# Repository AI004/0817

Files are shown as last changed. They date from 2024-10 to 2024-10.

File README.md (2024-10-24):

# 0817

## 网页版查看urdf模型方法

打开网页`https://gkjohnson.github.io/urdf-loaders/javascript/example/bundle/`

将目录`Drawing`下`robot_urdf_12DOF`或`robot_urdf_13DOF`文件夹整体拖入网页中即可打开模型

## webots仿真环境生成

### 步骤

1. 将`urdf`模型转换为`webots`模型，`solidworks`生成`urdf`模型时，`urdf`文件名字为`robot`，在导入`webots`操作时会有冲突

2. 参考`webots_world/adam_lite_simple`中`urdf`文件中，会有关于`world`和`floating_joint`的描述，但被注释，这是正确的，当调用各自目录下`urdf2proto.sh`脚步将`urdf`模型转换为`protos`时，`world`和`floating_joint`应被注释才能顺利执行

   #### 以`DuckDuck-13DOF`为例，执行成功时输出如下

        guobb@pndrobot-REN9000K:~/Documents/GBB/0817/webots_world/DuckDuck-13DOF$ sh urdf2proto.sh
        Robot name: DuckDuck
        Directory "./protos/DuckDuck_textures" already exists!
        Root link: base
        There are 14 links, 13 joints and 0 sensors

3. `webots`中点击`File`,点击`New`,点击`New Project Directory...`新建工程，右键`Add New`添加`PROTO nodes(Webots Projects)`下面`objects`中`floor`,右键`Add New`继续添加`PROTO nodes(Current Project)`中对应执行`urdf2proto.sh`脚步生成的要添加的机器人模型，本例中为`DuckDuck(Robot)`

4. 调整导入的模型在环境中的位置，避免穿模

5. 将生成的模型用于`Control`中时，除此之外，还需要适当修改，如`添加控制器`，`定义模型名称`，更改参考`meshs`文件路径，拷贝`meshs`和`urdf`文件至相应目录等

6. 在`webotsInterface.cpp`中修改`webots`的接口

7. 功能调试

## Control说明

1. 在`./Control/Webots/controllers/mpc_controller/src/webotsInterface.cpp`文件中这一行`Waist = robot->getFromDef("DuckDuck");`中修改模型名称，其中`"DuckDuck"`为`.wbt`文件中定义的机器人模型名称。如果想导入`PND`相关的机器人模型，将`"DuckDuck"`修改为`"Adam"`

2. `DuckDuck`腿部`DH`建模参考链接:<https://blog.csdn.net/qq_60580136/article/details/136062448>

## MatLab

1. 在MatLab计算过程中，计算的结果有 `6.1232e-17` 怎么处理，参考连接:<https://blog.csdn.net/jh1513/article/details/131243390>

2. MatLab计算左腿解析解分下

    1. 把所有变换矩阵都打印出来，参考MATRIX.txt文件
    2. 根据机器人的腿部结构，`关节123`可以抽象为一个`球关节`

        方案一：<span style="color: red; font-weight: bold;">failed</span>

            尝试把`关节123`相对于`base`的变换矩阵整合，观察得到的矩阵，可以看到`T14(3,3)`为`-cos(theta3)`，可以根据单一变量原则计算得到`theta3`，得到theta3后可以根据theta3得到其他，按照矩阵内数据分布可以得到全部的解析解

        方案二：尝试对最后一个变换矩阵求逆<span style="color: red; font-weight: bold;">failed</span>

            1. T16 * T7 = T17
            2. T16_temp = T17 * T7_inv
            3. T16 = T16_temp
            4. T16(3, 2) = cos(theta3)
            5. T16_temp(3, 2) = sin(theta7)
            6. sin(theta7) = cos(theta3)
            结论：
                theta3 = theta7 - pi/2
        方案三：参考链接:<https://blog.csdn.net/fengyu19930920/article/details/81144042> <span style="color: red; font-weight: bold;">failed</span>

            1. DuckDuck的腿部结构符合Pieper准则
            2. 参考UR机械臂逆解方法，把连续三个平行的关节的旋转矩阵单独拎出来，等号左边利用矩阵求逆，构建矩阵相等，观察数据

        方案四：改为MDH模型测试

## Log 说明

### DuckDuck对应的日志说明如下所示

1. 000~000:`时间(以0.0025s递增)`
2. 001~009:`程序内部各部分时间增量`
3. 010~018:`IMURPY角位置` `IMURPY角速度` `IMURPY角加速度`
4. 019~019:`0:start` `1:zero` `2:Z2S` `3:stand` `4:S2W` `5:walk` `6:UniGait` `7:Dual2Single` `8:SingleStand` `9:Single2Dual` `10:stop` `11:swing`
5. 020~020:`各状态时间`
6. 021~041:`q_a`
7. 042~062:`q_dot_a`
8. 063~083:`tau_a`
9. 084~095:`grf`
10. 096~116:`q_c`
11. 117~137:`q_dot_c`
12. 138~156:`tau_c`
13. 159~170:`contact_force`
14. 171~176:`left_foot_position`
15. 177~182:`left_foot_velocity`
16. 183~188:`right_foot_position`
17. 189~194:`right_foot_veloctiy`
18. 195~200:`com_position`
19. 201~206:`com_velocity`
20. 207~212:`body_position`
21. 213~218:`body_velocity`
22. 219~219:`motionTurnOn`
23. 220~220:`motionNumber`
24. 221~221:`momentumTurnOn`
25. 222~222:`carryBoxState`
26. 494~496:`v_body`
27. 497~499:`euler_world`

### DuckDuck对应的关节顺序

1. `left_hip_yaw_joint`
2. `left_hip_roll_joint`
3. `left_hip_pitch_joint`
4. `left_knee_pitch_joint`
5. `left_ankle_pitch_joint`
6. `left_ankle_roll_joint`
7. `right_hip_yaw_joint`
8. `right_hip_roll_joint`
9. `right_hip_pitch_joint`
10. `right_knee_pitch_joint`
11. `right_ankle_pitch_joint`
12. `right_ankle_roll_joint`
13. `throat_pitch_joint`
14. `throat_roll_joint`
15. `throat_yaw_joint`

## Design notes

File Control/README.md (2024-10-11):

## 各版本使用及注意事项描述

### webots可用版本
adam_lite.urdf

adam_standard.urdf

standard_plus23.urdf

standard_plus29.urdf

### 实机可用版本
adam_lite.urdf

adam_standard.urdf（未测试）

standard_plus23.urdf

standard_plus29.urdf

### urdf文件对应webots仿真环境描述
adam_lite.urdf - adam_lite_v1.1_world.wbt

adam_standard.urdf - adam_standard_world.wbt

standard_plus23.urdf - adma_standard_plus_23dof_world.wbt

standard_plus29.urdf - adma_standard_plus_29dof_world.wbt

standard_plus53.urdf - adma_standard_plus_53dof_world.wbt

### 使用方法
`webots` 仿真时更换`Sources/config/pnc_config_sim.json`中`"urdf"`标签即可

`实机运行时更换` Sources/config/pnc_config_sim.json中`"urdf"`标签即可

# 功能说明

## dataPub
添加dataPub模块，进行机器人状态数据发布。可在dataPub中添加自定义数据发布，实时监看更多机器人相关状态。具体话题发布于定义见`dataPub.cpp`。
`main.cpp`中使用`#define ROS_PUB`打开机器人数据话题发布。

## rqt_multiplot
安装对应ubuntu版本`rqt_multiplot`，启动`roscore`后，另起终端输入：
```
rqt_multiplot
```
打开`plot`文件夹中的.xml文件即可查看对应机器人状态绘图。在`dataPub.cpp`修改想要使用的话题与发布的数据相关，自定义.xml文件实现自己需求的数据实时绘图监看。

## example
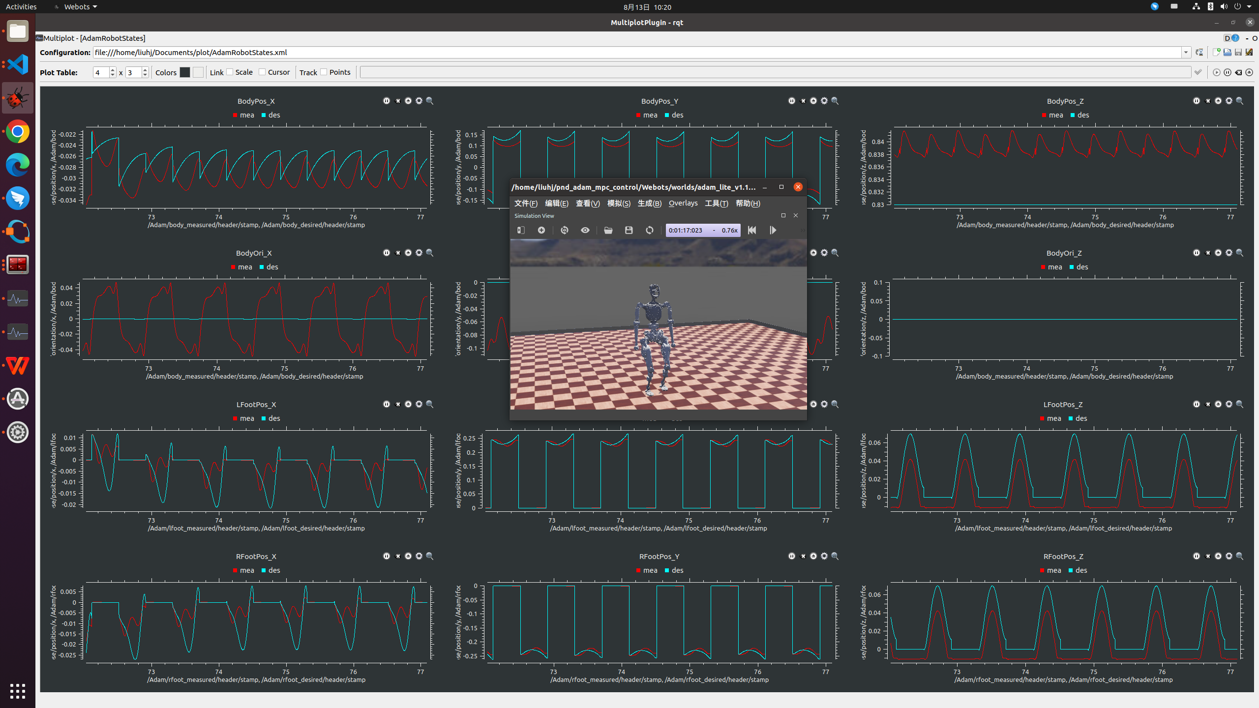
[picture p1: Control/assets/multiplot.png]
multiplot


## 基于角动量的落足点计算
首先使用rbdl进行质心处角动量计算，详见函数`estCOMStateMomentum()`,然后使用`footholdPlan_AM()`计算落足点。打开`pnc_config_sim.json`的`use_AM_calcFootHold`启用基于接触点角动量的落足点规划。同时新加入两个相关的落足点调整参数，`l_start_offset`,`r_start_offset`,加大该偏置可以调整落足点选取，调节以达到期望的侧向落足宽度。

## 角动量数据处理
收到外部干扰时角动量可能存在脉冲突变，使用一个中值滤波器进行脉冲处理，详见`updateDataAndProcessPulse`及`calculateMedian`函数。
真机上采集到的角动量数据噪音较大，故采用与`q_dot_a`同截止频率的低通滤波器进行滤波处理，打开`#define MOMENTUM_FILT`开关即可使用。

### reference
Gong, Yukai, and Jessy Grizzle. "Angular momentum about the contact point for control of bipedal locomotion: Validation in a lip-based controller." arXiv preprint arXiv:2008.10763 (2020).

Gong, Yukai, and Jessy W. Grizzle. "Zero dynamics, pendulum models, and angular momentum in feedback control of bipedal locomotion." Journal of Dynamic Systems, Measurement, and Control 144.12 (2022): 121006.

## push recovery
`state.cpp`中打开`momentumTurnOn`开关，打开`pnc_config_sim.json`的`use_AM_calcFootHold`开关。当机器人位于`stand`状态时，监测外力冲击及扰动，实时可切换进入`uniGait`状态，随后再切回站立状态。

### xbox
更新到使用xbox手柄切换`momentumTurnOn`开关，按下右摇杆按键即可切换。

#### xbox bug
手柄摇杆按键键值映射错误，已修正。
手柄键值存在抖动，状态切换时无影响，但是使用键值突变作为状态位切换时需注意锁存一个flag作为标志，防止抖动导致状态切换异常。

### world
新增一个添加有摆锤的仿真世界，世界名为`adma_standard_plus_23dof_withPendulum.wbt`，可从中复制摆锤添加到本地世界中使用。
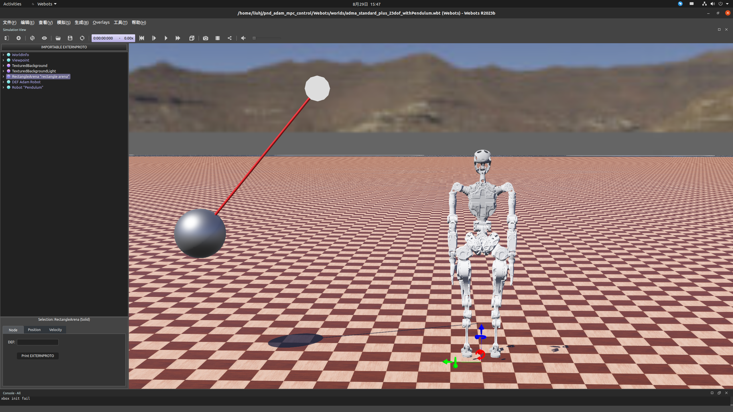
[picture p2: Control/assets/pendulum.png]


##
### 依赖环境
Eigen - https://gitlab.com/libeigen/eigen/-/archive/3.4.0/eigen-3.4.0.tar.gz

rbdl - https://github.com/rbdl/rbdl

qpOASES - https://github.com/coin-or/qpOASES.git

libtorch - https://download.pytorch.org/libtorch/cpu/libtorch-cxx11-abi-shared-with-deps-1.12.1%2Bcpu.zip

qt - sudo apt install qtbase5-dev

### 编译运行

#### Webots
编译： `sh buildwebotsim.sh`

清理： `sh cleanwebotsim.sh`

webots world: Webots/worlds/humanoid_test.wbt

#### 真机
编译： `sh buildrobot.sh`

清理： `sh cleanrobot.sh`

运行： `sh run.sh`

### 程序架构
#### example / Webots 
分别放置了上机和仿真的`main.cpp`

#### RobotControl:

`Robot_Constructor` 为机器人的RBDL建模

`Estimation_Operator`、`KalmanFilter` 为机器人的状态估计

`wbc_solver` 为WBC的求解

`MomentumController` 为原地抗干扰的动量控制

#### RobotInterface:

`JointInterface` 为关节控制接口

`S2P` 为脚踝的串并联转换

`wrist_S2P` 为手腕的串并联转换

`RobotInterfaceImpl` 为机器人获取状态和发送指令的具体实现，以及读绝编等

#### Sources

`joint_pd_config` 为关节的PD参数设置
`joint_abs_config` 为关节的零位
`pnc_config` 和 `pnc_config_sim` 分别是真机和仿真的WBC控制参数

`motion` 为原地动作的数据

`python_scripts` 为读绝编、设置零位的python脚本

#### StateMachine

`joystick` 为遥控器的代码

`State` 为回零、站立、行走等状态的具体实现

### 构型更改

在`Robot_Constructor`中调整`nbody`的数量，并参考现有代码填写新连杆的质心、重量惯量等参数

现有程序控制关节数量为23，将需要修改的地方替换成新关节数量

修改构型 WBC 控制算法一般无须调整，只要保证任务维度正确即可

### WBC控制

现有WBC采取对不同任务赋予不同权重的方式调整相对优先级，目前定义了5个任务：
`body_task` 为盆骨位姿任务，
`com_task` 为质心位姿任务，
`left_foot` 为左脚位姿任务，
`right_foot` 为右脚位姿任务，
`upper_joints` 为3个腰关节+8个手臂关节的关节角任务

其中盆骨、质心、左右脚的位姿均为工作空间的量，不因构型不同而变化，只需对上身关节角任务作相应调整

各任务的初始权重和PD参数在 `pnc_config` 中设定，在 `State.cpp` 各状态的 `OnEnter` 和 `run` 中会对各任务的权重做重新分配

KP/KD 1~6 的顺序是 roll pitch yaw x y z 

各关节的力矩上限和足底力上限通过 `WbcSolver::SetConstraints` 设定

`robotdata->q_a` `robotdata->q_dot_a` `robotdata->tau_a` 分别为关节的当前位置、速度和力矩

`robotdata->q_c` `robotdata->q_dot_c` `robotdata->tau_c` 分别为关节的期望位置、速度和力矩

`robotdata->q_factor` `robotdata->q_dot_factor` 分别为关节位置和速度的控制强度，从0到1控制强度逐渐变强

### Reference

Feng S, Whitman E, Xinjilefu X, et al. Optimization‐based full body control for the darpa robotics challenge[J]. Journal of field robotics, 2015, 32(2): 293-312.

Apgar T, Clary P, Green K, et al. Fast Online Trajectory Optimization for the Bipedal Robot Cassie[C]//Robotics: Science and Systems. 2018, 101: 14.

Moro F L, Sentis L. Whole-body control of humanoid robots[J]. Humanoid Robotics: A reference, Springer, Dordrecht, 2019.

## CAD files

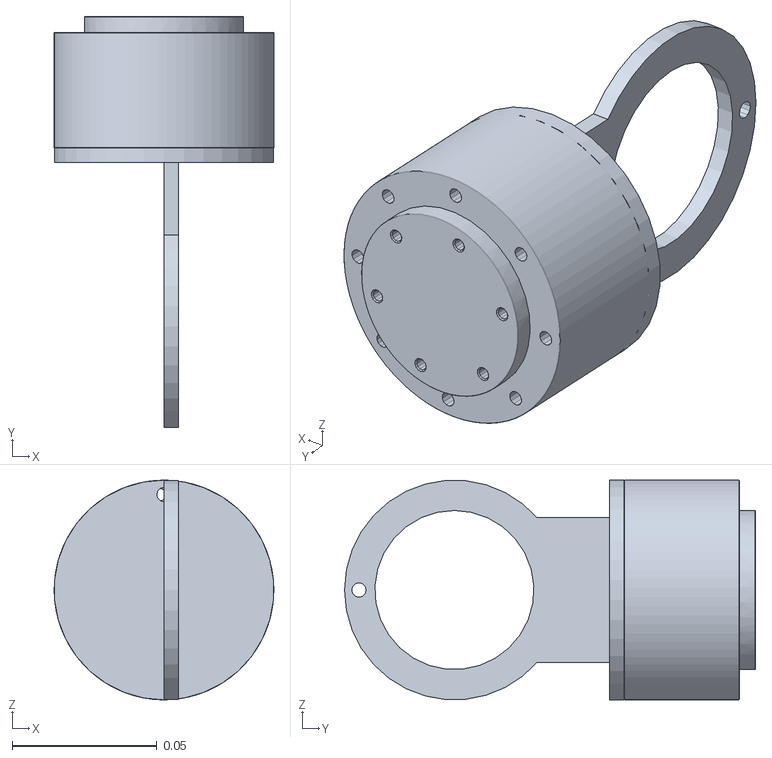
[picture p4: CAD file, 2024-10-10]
Control/Webots/meshes_DuckDuck/left_hip_roll.STL
0.076 x 0.142 x 0.076

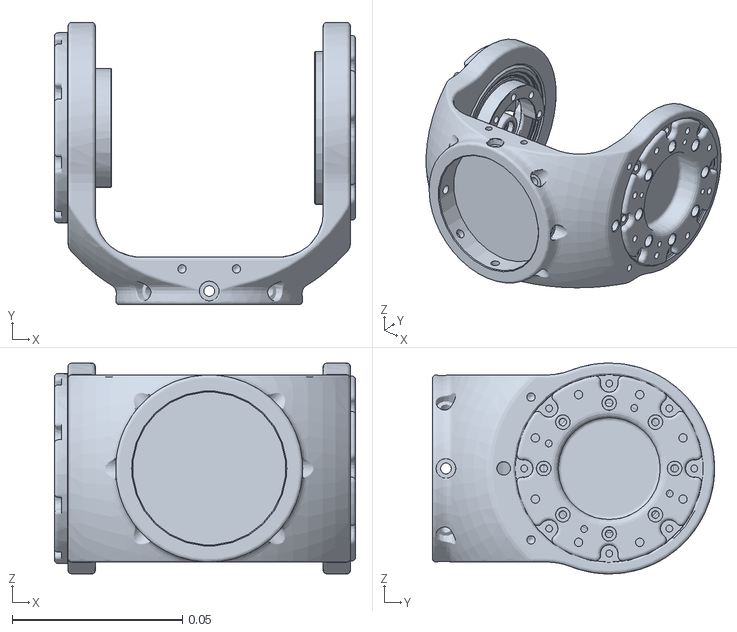
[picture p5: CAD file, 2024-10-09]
Control/Webots/meshes_lite_simple/shoulderPitchLeft.STL
0.0885 x 0.083 x 0.062

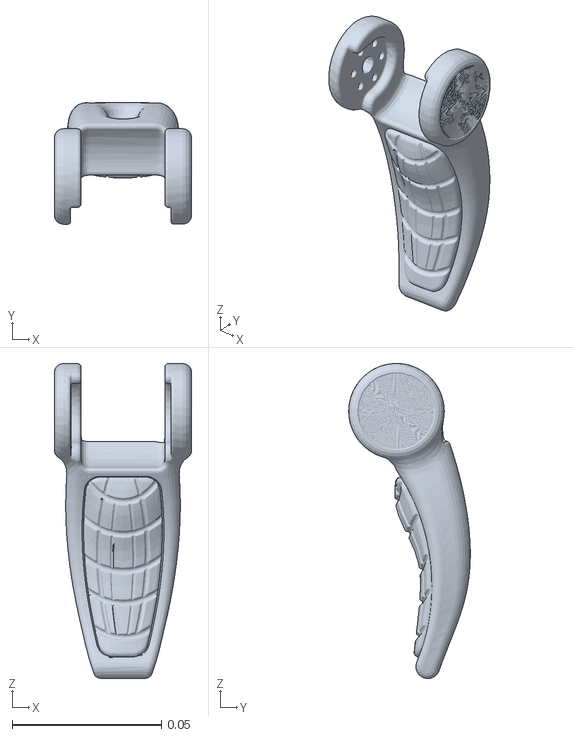
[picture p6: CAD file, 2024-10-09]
Control/Webots/meshes_standard/gripperRight.STL
0.046 x 0.0407 x 0.105

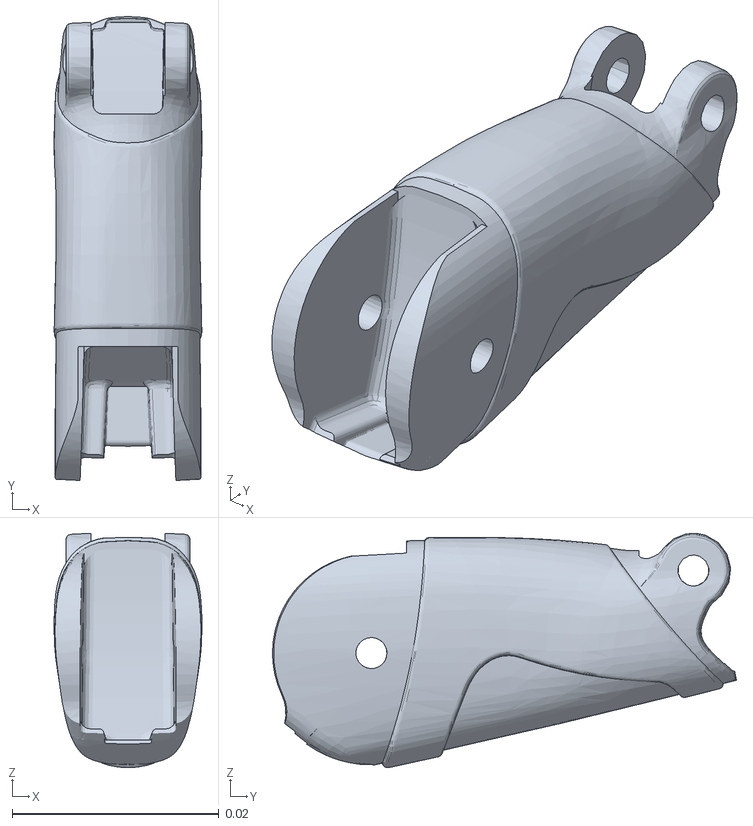
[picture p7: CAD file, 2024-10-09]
Control/Webots/meshes_standard_plus/R_ring_proximal.STL
0.0143 x 0.0449 x 0.0227

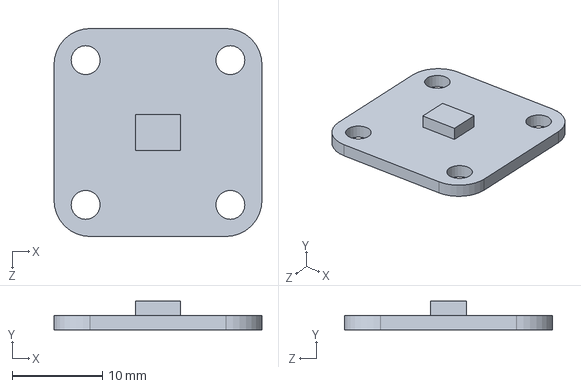
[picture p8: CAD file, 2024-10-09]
Drawing/branch struct/BLDC base/AS5600.SLDPRT
23.0 x 3.20 x 23.0 mm

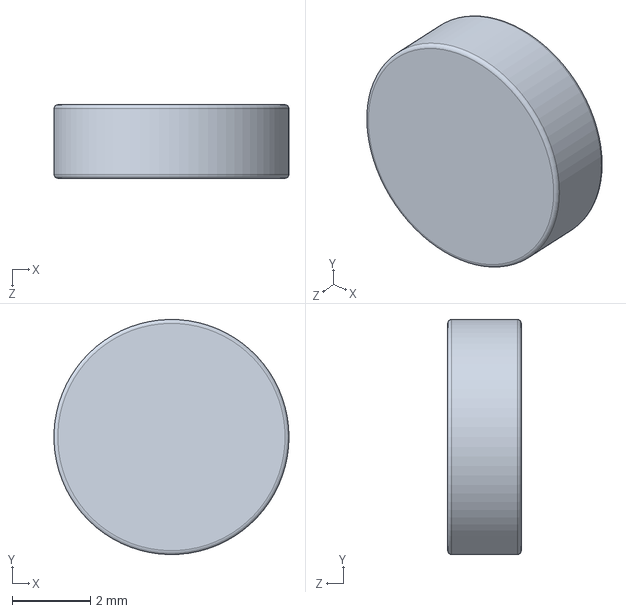
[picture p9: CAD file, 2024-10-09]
Drawing/branch struct/CycloidalDrive - v0.3.0/magnetic.SLDPRT
6.00 x 6.00 x 1.88 mm

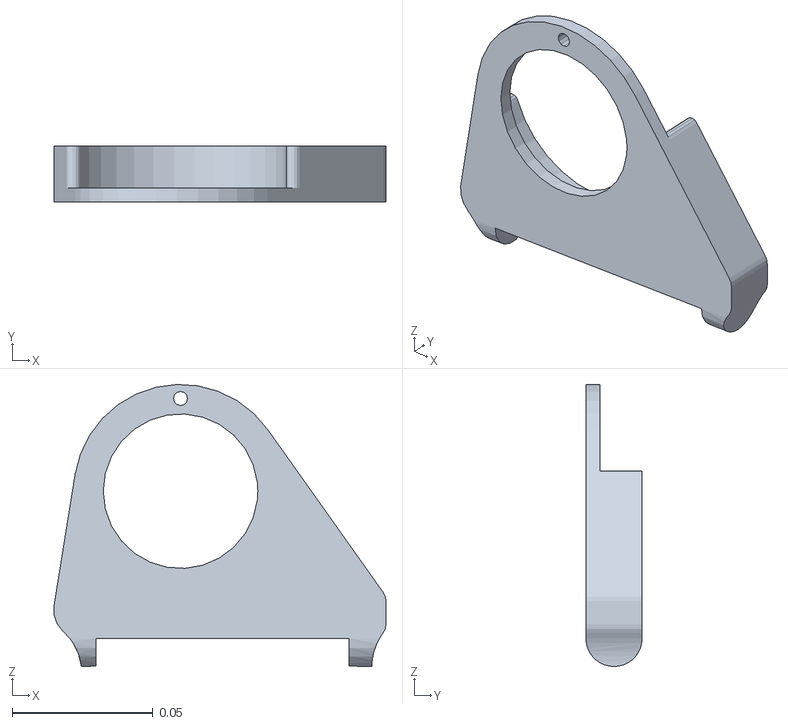
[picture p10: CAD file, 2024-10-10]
webots_world/DuckDuck-15DOF/meshes/right_ankle_pitch.STL
0.118 x 0.02 x 0.1

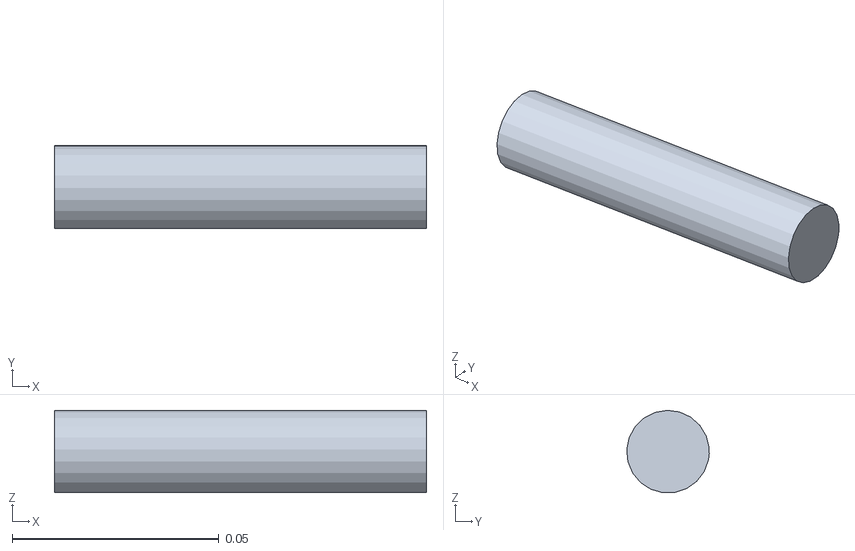
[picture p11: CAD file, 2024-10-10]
Control/Webots/meshes_DuckDuck/right_ankle_roll.STL
0.09 x 0.02 x 0.0199

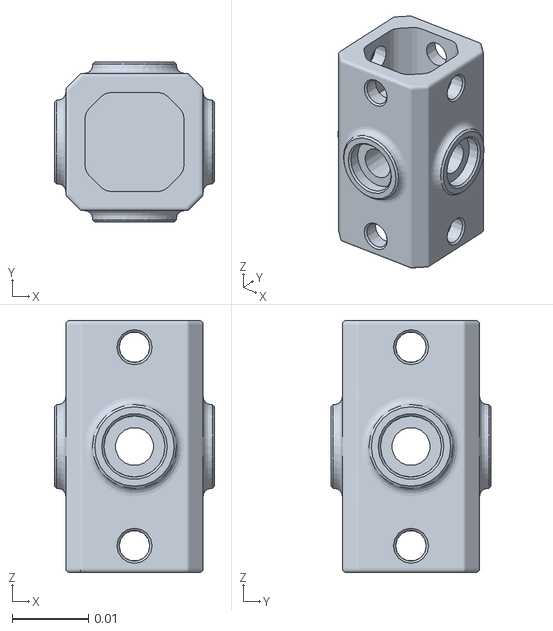
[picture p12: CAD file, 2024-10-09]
Control/Webots/meshes_lite_simple/anklePitchLeft.STL
0.021 x 0.021 x 0.033

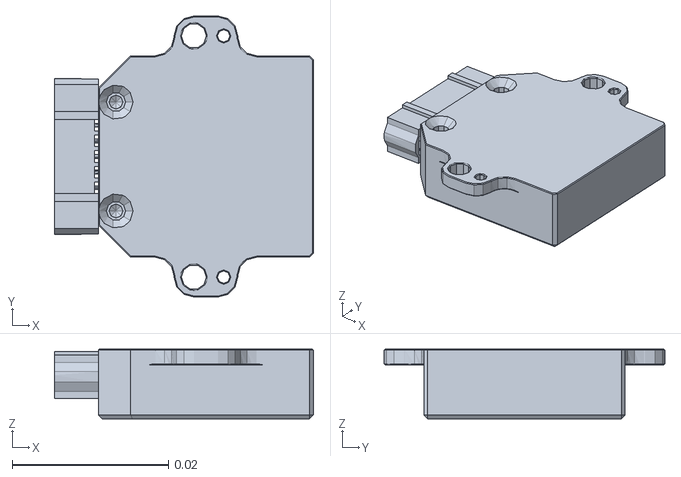
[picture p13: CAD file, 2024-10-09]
Control/Webots/meshes_standard/vn100-0001.stl
0.0331 x 0.0359 x 0.00892

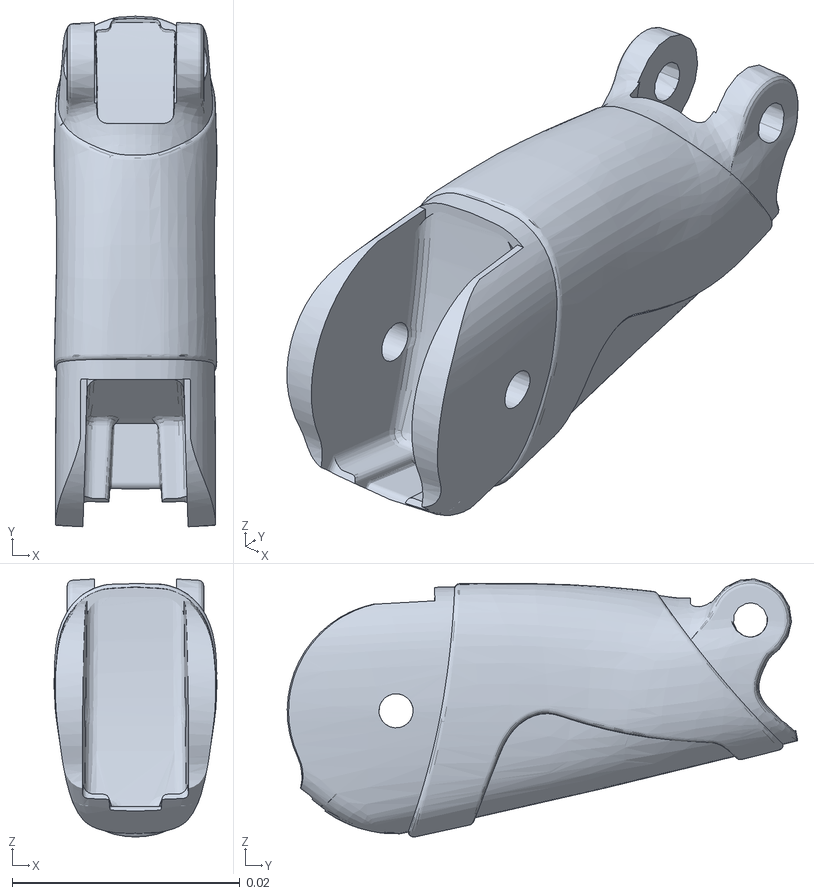
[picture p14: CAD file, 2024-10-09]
Control/Webots/meshes_standard_plus/R_index_distalR_middle_proximal.STL
0.0143 x 0.0449 x 0.0227

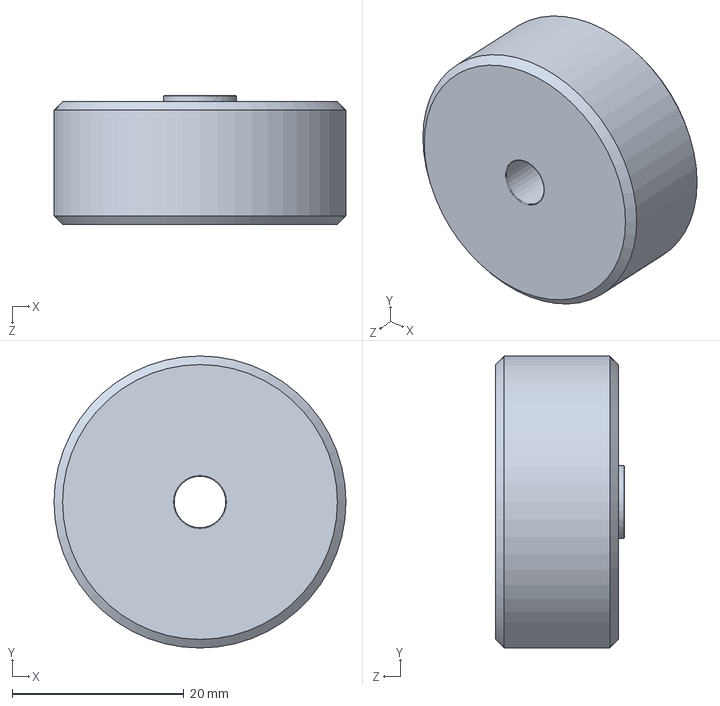
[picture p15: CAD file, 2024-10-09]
Drawing/branch struct/BLDC base/motor.SLDPRT
34.0 x 34.0 x 15.0 mm

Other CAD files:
Drawing/robot/DuckDuck.SLDASM
Drawing/branch struct/BLDC base/assembly.SLDASM
Drawing/robot/DuckDuck_Init_Position.SLDASM
Drawing/branch struct/CycloidalDrive - v0.3.0/装配体-总装.SLDASM
Drawing/branch struct/CycloidalDrive - v0.3.0/装配体-零件组合.SLDASM
Drawing/branch struct/CycloidalDrive - v0.3.0/装配体-爆炸结构.SLDASM
Control/Webots/meshes_DuckDuck/base.STL
Control/Webots/meshes_DuckDuck/left_ankle_pitch.STL
Control/Webots/meshes_DuckDuck/left_ankle_roll.STL
Control/Webots/meshes_DuckDuck/left_hip_pitch.STL
Control/Webots/meshes_DuckDuck/left_hip_yaw.STL
Control/Webots/meshes_DuckDuck/left_knee_pitch.STL
Control/Webots/meshes_DuckDuck/right_hip_pitch.STL
Control/Webots/meshes_DuckDuck/right_hip_roll.STL
Control/Webots/meshes_DuckDuck/right_hip_yaw.STL
Control/Webots/meshes_DuckDuck/throat_pitch.STL
Control/Webots/meshes_DuckDuck/throat_roll.STL
Control/Webots/meshes_DuckDuck/throat_yaw.STL
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

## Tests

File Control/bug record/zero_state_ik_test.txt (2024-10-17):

INFO: mpc_controller: Starting controller: /home/guobb/Documents/GBB/0817/Control/Webots/controllers/mpc_controller/mpc_controller
using urdf:./Sources/urdf/DuckDuck.urdf
DuckDuck
Bodies:
  Body ID: 0, Name: ROOT
  Body ID: 1, Name: base_Translate
  Body ID: 2, Name: base
  Body ID: 3, Name: left_hip_yaw
  Body ID: 4, Name: left_hip_roll
  Body ID: 5, Name: left_hip_pitch
  Body ID: 6, Name: left_knee_pitch
  Body ID: 7, Name: left_ankle_pitch
  Body ID: 8, Name: left_ankle_roll
  Body ID: 9, Name: neck_pitch
  Body ID: 10, Name: neck_roll
  Body ID: 11, Name: neck_yaw
  Body ID: 12, Name: right_hip_yaw
  Body ID: 13, Name: right_hip_roll
  Body ID: 14, Name: right_hip_pitch
  Body ID: 15, Name: right_knee_pitch
  Body ID: 16, Name: right_ankle_pitch
  Body ID: 17, Name: right_ankle_roll
robotdata->ndof: 21
robotdata->robot_model->mBodies.size(): 18
i: 0 2
i: 1 3
i: 2 4
i: 3 5
i: 4 6
i: 5 7
i: 6 8
i: 7 9
i: 8 10
i: 9 11
i: 10 12
i: 11 13
i: 12 14
i: 13 15
i: 14 16
i: 15 17
i: 16 18
i: 17 19
robotdata->task_card_set[0]->joint_id: 8
robotdata->task_card_set[1]->joint_id: 17
robotdata->task_card_set[2]->joint_id: 2
robotdata->task_card_set[3]->joint_id: 2
robotdata->task_card_set[4]->joint_id: 17
robotdata->task_card_set[5]->joint_id: 7
ndof: 21
Swing
Started 
xbox connect!
version: 1.4.0
Started!
To Zero
left leg jacobi:
           0            0            0            1            0  3.72529e-05  3.72529e-05            1  1.07986e-06  1.07986e-06  1.07986e-06            1            0            0            0            0            0            0            0            0            0
           0            0            0  2.06795e-25            1 -2.60325e-05 -2.60325e-05 -1.07803e-06            1            1            1 -1.07968e-06            0            0            0            0            0            0            0            0            0
           0            0            0  6.77626e-21  2.60325e-05            1            1 -3.72529e-05  4.89317e-05  4.89317e-05  4.89317e-05 -3.63101e-06            0            0            0            0            0            0            0            0            0
           1            0            0 -8.47033e-22     -0.33239    -0.133626   -0.0936258  3.84648e-06    -0.332392    -0.192392   -0.0523924 -1.27055e-21            0            0            0            0            0            0            0            0            0
           0            1            0     0.332387 -1.50978e-10  6.58279e-06  6.58283e-06     0.332388  3.58648e-07  2.07646e-07   5.6567e-08  2.95309e-17            0            0            0            0            0            0            0            0            0
           0            0            1     0.133634  5.79958e-06  4.97812e-06    3.488e-06    0.0936344  5.90069e-06  2.26128e-06  1.90237e-07  2.77556e-17            0            0            0            0            0            0            0            0            0
right leg jacobi:
           0            0            0            1            0  3.72529e-05            0            0            0            0            0            0            0            0            0 -3.72529e-05           -1  -1.1177e-05  -1.1177e-05  -1.1177e-05           -1
           0            0            0  2.06795e-25            1 -2.60325e-05            0            0            0            0            0            0            0            0            0  2.60325e-05 -1.11784e-05            1            1            1 -1.11783e-05
           0            0            0  6.77626e-21  2.60325e-05            1            0            0            0            0            0            0            0            0            0           -1  3.72526e-05  3.72444e-05  3.72444e-05  3.72444e-05  3.50987e-05
           1            0            0            0    -0.332393     0.133614            0            0            0            0            0            0            0            0            0   -0.0936144   7.2027e-06    -0.332392    -0.192392   -0.0523924  4.23516e-22
           0            1            0     0.332397  -2.8436e-10  1.45948e-06            0            0            0            0            0            0            0            0            0 -1.45944e-06    -0.332396 -3.71559e-06 -2.15062e-06 -5.85657e-07  1.12154e-17
           0            0            1    -0.133606  1.09233e-05 -4.97748e-06            0            0            0            0            0            0            0            0            0  3.48737e-06    0.0936058  1.19695e-05  6.75342e-06   1.8389e-06  2.77556e-17
head jacobi:
0 0 0 0 0 0 0 0 0 0 0 0 1 0 0 0 0 0 0 0 0
0 0 0 0 0 0 0 0 0 0 0 0 0 1 0 0 0 0 0 0 0
0 0 0 0 0 0 0 0 0 0 0 0 0 0 1 0 0 0 0 0 0

==============================================================================================================================
==============================================================VS==============================================================
==============================================================================================================================

model->dof_count: 21
model->mBodies.size(): 18
model->gravity:     0     0 -9.81
Joints:
  ROOT
  base_Translate
  base
  left_hip_yaw
  left_hip_roll
  left_hip_pitch
  left_knee_pitch
  left_ankle_pitch
  left_ankle_roll
  neck_pitch
  neck_roll
  neck_yaw
  right_hip_yaw
  right_hip_roll
  right_hip_pitch
  right_knee_pitch
  right_ankle_pitch
  right_ankle_roll
Bodies:
  Body ID: 0, Name: ROOT
  Body ID: 1, Name: base_Translate
  Body ID: 2, Name: base
  Body ID: 3, Name: left_hip_yaw
  Body ID: 4, Name: left_hip_roll
  Body ID: 5, Name: left_hip_pitch
  Body ID: 6, Name: left_knee_pitch
  Body ID: 7, Name: left_ankle_pitch
  Body ID: 8, Name: left_ankle_roll
  Body ID: 9, Name: neck_pitch
  Body ID: 10, Name: neck_roll
  Body ID: 11, Name: neck_yaw
  Body ID: 12, Name: right_hip_yaw
  Body ID: 13, Name: right_hip_roll
  Body ID: 14, Name: right_hip_pitch
  Body ID: 15, Name: right_knee_pitch
  Body ID: 16, Name: right_ankle_pitch
  Body ID: 17, Name: right_ankle_roll
Q: 0 0 0 0 0 0 0 0 0 0 0 0 0 0 0 0 0 0 0 0 0
QDot: 0 0 0 0 0 0 0 0 0 0 0 0 0 0 0 0 0 0 0 0 0
Tau: 0 0 0 0 0 0 0 0 0 0 0 0 0 0 0 0 0 0 0 0 0
QDDot:  2.22045e-16 -1.38778e-17        -9.81 -7.07298e-17  -6.6653e-16 -1.08278e-17  1.99807e-15   9.5483e-17  1.06981e-15 -4.55485e-16 -9.72608e-17 -2.47532e-17 -1.76993e-16 -5.64579e-17  1.03078e-17  2.01833e-15 -1.51671e-16  1.03713e-15 -4.20304e-16 -1.29301e-16  8.09414e-17
Q: 0 0 0 0 0 0 0 0 0 0 0 0 0 0 0 0 0 0 0 0 0
QDot: 0 0 0 0 0 0 0 0 0 0 0 0 0 0 0 0 0 0 0 0 0
Tau:  4.95859e-16 -3.44709e-17  5.25285e-17 -5.29631e-34  4.10464e-33 -5.00742e-33 -1.92593e-33 -2.94908e-34 -1.46175e-33  4.81482e-35  2.25695e-36 -2.18328e-39  7.02964e-33 -7.89932e-35 -6.77085e-36  4.81482e-34  7.46298e-34  1.32144e-33            0  5.64237e-36 -1.26091e-38
QDDot:  2.22045e-16 -1.38778e-17        -9.81 -7.07298e-17  -6.6653e-16 -1.08278e-17  1.99807e-15   9.5483e-17  1.06981e-15 -4.55485e-16 -9.72608e-17 -2.47532e-17 -1.76993e-16 -5.64579e-17  1.03078e-17  2.01833e-15 -1.51671e-16  1.03713e-15 -4.20304e-16 -1.29301e-16  8.09414e-17
Body Transform (Base to Body 8):
        1         0         0         0
        0         1         0  0.133618
        0         0         1 -0.332392
        0         0         0         1
Jacobian Matrix (Body 8):
         0          0          0          1          0          0          0          1          0          0          0          1          0          0          0          0          0          0          0          0          0
         0          0          0          0          1          0          0          0          1          1          1          0          0          0          0          0          0          0          0          0          0
         0          0          0          0          0          1          1          0          0          0          0          0          0          0          0          0          0          0          0          0          0
         1          0          0          0  -0.332392  -0.133618 -0.0936182          0  -0.332392  -0.192392 -0.0523924          0          0          0          0          0          0          0          0          0          0
         0          1          0   0.332392          0          0          0   0.332392          0          0          0          0          0          0          0          0          0          0          0          0          0
         0          0          1   0.133618          0          0          0  0.0936182          0          0          0          0          0          0          0          0          0          0          0          0          0
Jacobian Matrix (Body 17):
         0          0          0          1          0          0          0          0          0          0          0          0          0          0          0          0         -1          0          0          0         -1
         0          0          0          0          1          0          0          0          0          0          0          0          0          0          0          0          0          1          1          1          0
         0          0          0          0          0          1          0          0          0          0          0          0          0          0          0         -1          0          0          0          0          0
         1          0          0          0  -0.332392   0.133618          0          0          0          0          0          0          0          0          0 -0.0936182          0  -0.332392  -0.192392 -0.0523924          0
         0          1          0   0.332392          0          0          0          0          0          0          0          0          0          0          0          0  -0.332392          0          0          0          0
         0          0          1  -0.133618          0          0          0          0          0          0          0          0          0          0          0          0  0.0936182          0          0          0          0
Jacobian Matrix (Body 11):
     0      0      0      0      0      0 0.0025      0      0      0      0      0      0 0.1385      0      0      0      0      0      0      0
     0      0      0      0      1      0 0.0775      0      0      0      0      0      1      0  0.061      0      0      0      0      0      0
     0      0      0      1      0      1      0      0      0      0      0      0      0      0      0      0      0      0      0      0      0
model->q_size: 21
error: 0.148857  0.0811659   0.119197  0.0284271 -0.0144422     0.0154  0.0104289
error: 0.0279139         0.00167909  -0.0043331   0.0274701 0.000301794 0.000831977 -0.00148235
error: 0.0101265          0.00681823  -0.00741633  -0.00101897  8.48899e-06 -4.85448e-05 -0.000120378
error: 0.00206528        0.000235621 -3.20301e-06  -0.00205179 -5.53563e-07  1.15344e-07 -2.16779e-06
error: 0.000729142      -0.000479004  0.000549417 -1.85808e-05 -3.54857e-08 -2.86412e-07 -1.78004e-07
error: 0.000158336      -4.00638e-05  2.49869e-05  0.000151132 -2.14527e-09  -1.0211e-09 -1.37429e-08
error: 5.25969e-05       3.37228e-05 -3.95292e-05  8.16398e-06 -2.09217e-10  -1.3553e-09 -1.06313e-09
error: 1.22543e-05       4.47633e-06 -3.62638e-06 -1.08158e-05 -1.17184e-11 -2.30812e-11 -6.94363e-11
error: 3.75225e-06      -2.29376e-06  2.76204e-06 -1.09049e-06 -1.16395e-12 -5.97994e-12 -6.23163e-12
error: 9.52502e-07      -4.34401e-07  3.92544e-07  7.51309e-07 -6.28317e-14 -2.41973e-13 -3.51608e-13
Inverse Kinematics Converged in 9 iterations.
Function took 0.616268 milliseconds
Inverse Kinematics Result:   0.14966  0.150027 -0.449909   0.50081  0.147031  0.149633

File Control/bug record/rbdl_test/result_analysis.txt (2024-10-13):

-- Found RBDL: /usr/local/lib/librbdl.so
-- Configuring done
-- Generating done
-- Build files have been written to: /home/g/Documents/0817/Control/bug record/rbdl_test/build
Scanning dependencies of target read_urdf
[ 25%] Building CXX object CMakeFiles/read_urdf.dir/read_urdf.cpp.o
[ 75%] Built target example
[100%] Linking CXX executable read_urdf
[100%] Built target read_urdf
model->dof_count: 21
model->mBodies.size(): 18
model->gravity:     0     0 -9.81
Joints:
  ROOT
  base_Translate
  base
  left_hip_yaw
  left_hip_roll
  left_hip_pitch
  left_knee_pitch
  left_ankle_pitch
  left_ankle_roll
  neck_pitch
  neck_roll
  neck_yaw
  right_hip_yaw
  right_hip_roll
  right_hip_pitch
  right_knee_pitch
  right_ankle_pitch
  right_ankle_roll
Bodies:
  Body ID: 0, Name: ROOT
  Body ID: 1, Name: base_Translate
  Body ID: 2, Name: base
  Body ID: 3, Name: left_hip_yaw
  Body ID: 4, Name: left_hip_roll
  Body ID: 5, Name: left_hip_pitch
  Body ID: 6, Name: left_knee_pitch
  Body ID: 7, Name: left_ankle_pitch
  Body ID: 8, Name: left_ankle_roll
  Body ID: 9, Name: neck_pitch
  Body ID: 10, Name: neck_roll
  Body ID: 11, Name: neck_yaw
  Body ID: 12, Name: right_hip_yaw
  Body ID: 13, Name: right_hip_roll
  Body ID: 14, Name: right_hip_pitch
  Body ID: 15, Name: right_knee_pitch
  Body ID: 16, Name: right_ankle_pitch
  Body ID: 17, Name: right_ankle_roll
Q: 0 0 0 0 0 0 0 0 0 0 0 0 0 0 0 0 0 0 0 0 0
QDot: 0 0 0 0 0 0 0 0 0 0 0 0 0 0 0 0 0 0 0 0 0
Tau: 0 0 0 0 0 0 0 0 0 0 0 0 0 0 0 0 0 0 0 0 0
QDDot:  2.22045e-16 -1.38778e-17        -9.81 -7.07298e-17  -6.6653e-16 -1.08278e-17  1.99807e-15   9.5483e-17  1.06981e-15 -4.55485e-16 -9.72608e-17 -2.47532e-17 -1.76993e-16 -5.64579e-17  1.03078e-17 -2.01833e-15  1.51671e-16 -1.03713e-15  4.20304e-16  1.29301e-16 -8.09414e-17
Q: 0 0 0 0 0 0 0 0 0 0 0 0 0 0 0 0 0 0 0 0 0
QDot: 0 0 0 0 0 0 0 0 0 0 0 0 0 0 0 0 0 0 0 0 0
Tau:  4.95859e-16 -3.44709e-17  5.25285e-17 -5.29631e-34  4.10464e-33 -5.00742e-33 -1.92593e-33 -2.94908e-34 -1.46175e-33  4.81482e-35  2.25695e-36 -2.18328e-39  7.02964e-33 -7.89932e-35 -6.77085e-36 -4.81482e-34 -7.46298e-34 -1.32144e-33           -0 -5.64237e-36  1.26091e-38
QDDot:  2.22045e-16 -1.38778e-17        -9.81 -7.07298e-17  -6.6653e-16 -1.08278e-17  1.99807e-15   9.5483e-17  1.06981e-15 -4.55485e-16 -9.72608e-17 -2.47532e-17 -1.76993e-16 -5.64579e-17  1.03078e-17 -2.01833e-15  1.51671e-16 -1.03713e-15  4.20304e-16  1.29301e-16 -8.09414e-17
Body Transform (Base to Body 11):
       1        0        0   0.0775
       0        1        0  -0.0025
       0        0        1 0.247375
       0        0        0        1
Jacobian Matrix (Body 11):
        1         0         0         0  0.247375    0.0025         0         0         0         0         0         0    0.1385         0         0         0         0         0         0         0         0
        0         1         0 -0.247375         0    0.0775         0         0         0         0         0         0         0     0.061         0         0         0         0         0         0         0
        0         0         1   -0.0025   -0.0775         0         0         0         0         0         0         0         0         0         0         0         0         0         0         0         0
        0         0         0         0         0         0         0         0         0         0         0         0         0         0         0         0         0         0         0         0         0
        0         0         0         0         0         0         0         0         0         0         0         0         0         0         0         0         0         0         0         0         0
        0         0         0         0         0         0         0         0         0         0         0         0         0         0         0         0         0         0         0         0         0
read_urdf: /usr/local/include/eigen3/Eigen/src/Core/SolverBase.h:151: void Eigen::SolverBase<Derived>::_check_solve_assertion(const Rhs&) const [with bool Transpose_ = false; Rhs = Eigen::MatrixBase<Eigen::Matrix<double, 3, 1> >; Derived = Eigen::ColPivHouseholderQR<Eigen::Matrix<double, -1, -1, 1, -1, -1> >]: Assertion `(Transpose_?derived().cols():derived().rows())==b.rows() && "SolverBase::solve(): invalid number of rows of the right hand side matrix b"' failed.
Aborted (core dumped)
g@g:~/Documents/0817/Control/bug record/rbdl_test$

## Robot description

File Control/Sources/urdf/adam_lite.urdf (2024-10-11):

<?xml version="1.1" encoding="utf-8"?>
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
<robot name="adam_lite">
  <link name="world"/>
  <link name="pelvis">
    <inertial>
      <origin xyz="-0.00120281 -0.00000119 -0.00802155" rpy="0 0 0" />
      <mass value="10.18730021" />
      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
    </inertial>
    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
  </link>
  <joint name="floating_joint" type="floating">
    <parent link="world"/> 
    <child link="pelvis"/>
    <origin xyz="0 0 0" rpy="0 0 0"/>
    <axis xyz="0 0 0 1 0 0" />
    <axis xyz="0 0 0 0 1 0" />
    <axis xyz="0 0 0 0 0 1" />
    <axis xyz="1 0 0" />
    <axis xyz="0 1 0" />
    <axis xyz="0 0 1" />
  </joint>
  <link name="hipPitchLeft">
    <inertial>
      <origin xyz="-0.05818187 0.05889478 -0.00031205" rpy="0 0 0" />
      <mass value="2.15124786" />
      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
    </inertial>
    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
  </link>
  <joint name="hipPitch_Left" type="revolute">
    <origin xyz="0 0.096192 -0.033241" rpy="-0.61087 0 0" />
    <parent link="pelvis" />
    <child link="hipPitchLeft" />
    <axis xyz="0 1 0" />
    <limit effort="230.0" lower="-2.09" upper="2.09" velocity="15.0"/>
  </joint>
  <link name="hipRollLeft">
    <inertial>
      <origin xyz="0.03995412 -0.00011618 -0.01102103" rpy="0 0 0" />
      <mass value="1.29421887" />
      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
    </inertial>
    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
  </link>
  <joint name="hipRoll_Left" type="revolute">
    <origin xyz="-0.0255 0.069 0" rpy="0.61087 0 0" />
    <parent link="hipPitchLeft" />
    <child link="hipRollLeft" />
    <axis xyz="1 0 0" />
    <limit effort="160.0" lower="-0.78" upper="1.57" velocity="8.0"/>
  </joint>
  <link name="thighLeft">
    <inertial>
      <origin xyz="0.00331195 -0.01112470 -0.13519832" rpy="0 0 0" />
      <mass value="6.64749717" />
      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
    </inertial>
    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
  </link>
  <joint name="hipYaw_Left" type="revolute">
    <origin xyz="0.044 0 -0.0525" rpy="0 0 0" />
    <parent link="hipRollLeft" />
    <child link="thighLeft" />
    <axis xyz="0 0 1" />
    <limit effort="105" lower="-0.78" upper="0.78" velocity="8.0"/>
  </joint>
  <link name="shinLeft">
    <inertial>
      <origin xyz="-0.00080913 0.00097265 -0.14540818" rpy="0 0 0" />
      <mass value="2.19866469" />
      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
    </inertial>
    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
  </link>
  <joint name="kneePitch_Left" type="revolute">
    <origin xyz="0 -0.0355 -0.369" rpy="0 0 0" />
    <parent link="thighLeft" />
    <child link="shinLeft" />
    <axis xyz="0 1 0" />
    <limit effort="230.0" lower="-0.09" upper="2.4" velocity="15.0"/>
  </joint>
  <link name="anklePitchLeft">
    <inertial>
      <origin xyz="0.00000000 0.00000000 0.00000000" rpy="0 0 0" />
      <mass value="0.03100000" />
      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
    </inertial>
    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
  </link>
  <joint name="anklePitch_Left" type="revolute">
    <origin xyz="0 0 -0.37" rpy="0 0 0" />
    <parent link="shinLeft" />
    <child link="anklePitchLeft" />
    <axis xyz="0 1 0" />
    <limit effort="40.0" lower="-1.0" upper="0.35" velocity="20.0"/>
  </joint>
  <link name="toeLeft">
    <inertial>
      <origin xyz="0.03700657 -0.00002063 -0.04198684" rpy="0 0 0" />
      <mass value="0.47580000" />
      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
    </inertial>
    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
  </link>
  <joint name="ankleRoll_Left" type="revolute">
    <origin xyz="0 0 0" rpy="0 0 0" />
    <parent link="anklePitchLeft" />
    <child link="toeLeft" />
    <axis xyz="1 0 0" />
    <limit effort="12.0" lower="-0.3491" upper="0.3491" velocity="20.0"/>
  </joint>
  <link name="hipPitchRight">
    <inertial>
      <origin xyz="-0.05818164 -0.05886958 -0.00032981" rpy="0 0 0" />
      <mass value="2.15124254" />
      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
    </inertial>
    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
  </link>
  <joint name="hipPitch_Right" type="revolute">
    <origin xyz="0 -0.096192 -0.033241" rpy="0.61087 0 0" />
    <parent link="pelvis" />
    <child link="hipPitchRight" />
    <axis xyz="0 1 0" />
    <limit effort="230.0" lower="-2.09" upper="2.09" velocity="15.0"/>
  </joint>
  <link name="hipRollRight">
    <inertial>
      <origin xyz="0.03988167 0.00011594 -0.01102087" rpy="0 0 0" />
      <mass value="1.29422777" />
      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
    </inertial>
    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
  </link>
  <joint name="hipRoll_Right" type="revolute">
    <origin xyz="-0.0255 -0.069 0" rpy="-0.61087 0 0" />
    <parent link="hipPitchRight" />
    <child link="hipRollRight" />
    <axis xyz="1 0 0" />
    <limit effort="160.0" lower="-1.57" upper="0.78" velocity="8.0"/>
  </joint>
  <link name="thighRight">
    <inertial>
      <origin xyz="0.00332701 0.01110269 -0.13528959" rpy="0 0 0" />
      <mass value="6.64754534" />
      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
    </inertial>
    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
  </link>
  <joint name="hipYaw_Right" type="revolute">
    <origin xyz="0.044 0 -0.0525" rpy="0 0 0" />
    <parent link="hipRollRight" />
    <child link="thighRight" />
    <axis xyz="0 0 1" />
    <limit effort="105" lower="-0.78" upper="0.78" velocity="8.0"/>
  </joint>
  <link name="shinRight">
    <inertial>
      <origin xyz="-0.00079979 -0.00097288 -0.14635087" rpy="0 0 0" />
      <mass value="2.20809154" />
      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
    </inertial>
    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
  </link>
  <joint name="kneePitch_Right" type="revolute">
    <origin xyz="0 0.0355 -0.369" rpy="0 0 0" />
    <parent link="thighRight" />
    <child link="shinRight" />
    <axis xyz="0 1 0" />
    <limit effort="230.0" lower="-0.09" upper="2.4" velocity="15.0"/>
  </joint>
  <link name="anklePitchRight">
    <inertial>
      <origin xyz="0.00000000 0.00000000 0.00000000" rpy="0 0 0" />
      <mass value="0.03100000" />
      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
    </inertial>
    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
  </link>
  <joint name="anklePitch_Right" type="revolute">
    <origin xyz="0 0 -0.37" rpy="0 0 0" />
    <parent link="shinRight" />
    <child link="anklePitchRight" />
    <axis xyz="0 1 0" />
    <limit effort="40.0" lower="-1.0" upper="0.35" velocity="20.0"/>
  </joint>
  <link name="toeRight">
    <inertial>
      <origin xyz="0.03700297 0.00002151 -0.04197563" rpy="0 0 0" />
      <mass value="0.47580000" />
      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
    </inertial>
    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
  </link>
  <joint name="ankleRoll_Right" type="revolute">
    <origin xyz="0 0 0" rpy="0 0 0" />
    <parent link="anklePitchRight" />
    <child link="toeRight" />
    <axis xyz="1 0 0" />
    <limit effort="12.0" lower="-0.3491" upper="0.3491" velocity="20.0"/>
  </joint>
  <link name="waistRoll">
    <inertial>
      <origin xyz="0.00212014 0.00212051 0.03999987" rpy="0 0 0" />
      <mass value="2.18430742" />
      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
    </inertial>
    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
  </link>
  <joint name="waistRoll" type="revolute">
    <origin xyz="0 0 0.044" rpy="0 0 0" />
    <parent link="pelvis" />
    <child link="waistRoll" />
    <axis xyz="1 0 0" />
    <limit effort="110" lower="-0.52" upper="0.52" velocity="8.0"/>
  </joint>
  <link name="waistPitch">
    <inertial>
      <origin xyz="-0.00066627 0.00070478 0.02506554" rpy="0 0 0" />
      <mass value="0.49870000" />
      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
    </inertial>
    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
  </link>
  <joint name="waistPitch" type="revolute">
    <origin xyz="0 0 0.08" rpy="0 0 0" />
    <parent link="waistRoll" />
    <child link="waistPitch" />
    <axis xyz="0 1 0" />
    <limit effort="110" lower="-0.78" upper="0.78" velocity="8.0"/>
  </joint>
  <link name="torso">
    <inertial>
      <origin xyz="0.00080019 -0.00003149 0.18300318" rpy="0 0 0" />
      <mass value="13.28595962" />
      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
    </inertial>
    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
  </link>
  <joint name="waistYaw" type="revolute">
    <origin xyz="0 0.0005 0.053" rpy="0 0 0" />
    <parent link="waistPitch" />
    <child link="torso" />
    <axis xyz="0 0 1" />
    <limit effort="110" lower="-0.78" upper="0.78" velocity="8.0"/>
  </joint>
  <link name="shoulderPitchLeft">
    <inertial>
      <origin xyz="-0.00150404 0.02688841 0.00010848" rpy="0 0 0" />
      <mass value="0.20310000" />
      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
    </inertial>
    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
  </link>
  <joint name="shoulderPitch_Left" type="revolute">
    <origin xyz="0 0.16011 0.25742" rpy="0.34907 0 0" />
    <parent link="torso" />
    <child link="shoulderPitchLeft" />
    <axis xyz="0 1 0" />
    <limit effort="65.0" lower="-2.7" upper="1.0" velocity="8.0"/>
  </joint>
  <link name="shoulderRollLeft">
    <inertial>
      <origin xyz="-0.02860447 0.01104245 -0.01405309" rpy="0 0 0" />
      <mass value="0.72480000" />
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

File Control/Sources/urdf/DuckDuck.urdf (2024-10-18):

<?xml version="1.0" encoding="utf-8"?>
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
<robot name="DuckDuck">
  <link name="world"/>
  <joint name="floating_joint" type="floating">
    <parent link="world"/>
    <child link="base"/>
    <origin xyz="0 0 0" rpy="0 0 0"/>
    <axis xyz="0 0 0 1 0 0" />
    <axis xyz="0 0 0 0 1 0" />
    <axis xyz="0 0 0 0 0 1" />
    <axis xyz="1 0 0" />
    <axis xyz="0 1 0" />
    <axis xyz="0 0 1" />
  </joint>
  <link name="base">
    <inertial>
      <origin xyz="-0.0100928530626795 -8.48766786223073E-05 0.0417109438407734" rpy="0 0 0" />
      <mass value="1.70037419863104" />
      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
    </inertial>
    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
  </link>
  <link name="left_hip_yaw">
    <inertial>
      <origin xyz="-0.0148415027804522 -1.42278207789504E-05 0.00518098759586325" rpy="0 0 0" />
      <mass value="0.22770651071542" />
      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
    </inertial>
    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
  </link>
  <joint name="left_hip_yaw_joint" type="revolute">
    <origin xyz="0 0.04 0" rpy="0 0 0" />
    <parent link="base" />
    <child link="left_hip_yaw" />
    <axis xyz="0 0 1" />
    <limit lower="-2" upper="2" effort="20" velocity="15.0" />
  </joint>
  <link name="left_hip_roll">
    <inertial>
      <origin xyz="0.00016868655630813 0.0732538542750924 -1.42428991139337E-05" rpy="0 0 0" />
      <mass value="0.22746544778837" />
      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
    </inertial>
    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
  </link>
  <joint name="left_hip_roll_joint" type="revolute">
    <origin xyz="0 0 0" rpy="0 0 0" />
    <parent link="left_hip_yaw" />
    <child link="left_hip_roll" />
    <axis xyz="1 0 0" />
    <limit lower="-2" upper="2" effort="20" velocity="15.0" />
  </joint>
  <link name="left_hip_pitch">
    <inertial>
      <origin xyz="-3.35688425254106E-16 0.0845594117245176 -0.125225619873394" rpy="0 0 0" />
      <mass value="0.24023854356995" />
      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
    </inertial>
    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
  </link>
  <joint name="left_hip_pitch_joint" type="revolute">
    <origin xyz="0 0 0" rpy="0 0 0" />
    <parent link="left_hip_roll" />
    <child link="left_hip_pitch" />
    <axis xyz="0 1 0" />
    <limit lower="-2" upper="2" effort="20" velocity="15.0" />
  </joint>
  <link name="left_knee_pitch">
    <inertial>
      <origin xyz="-3.14931093635428E-16 -0.00857325265941741 -0.127010278601144" rpy="0 0 0" />
      <mass value="0.232718078417979" />
      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
    </inertial>
    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
  </link>
  <joint name="left_knee_pitch_joint" type="revolute">
    <origin xyz="0 0.0936181760425075 -0.14" rpy="0 0 0" />
    <parent link="left_hip_pitch" />
    <child link="left_knee_pitch" />
    <axis xyz="0 1 0" />
    <limit lower="-2" upper="2" effort="20" velocity="15.0" />
  </joint>
  <link name="left_ankle_pitch">
    <inertial>
      <origin xyz="0.0171971119634686 0.00125991692727168 -0.027457582228249" rpy="0 0 0" />
      <mass value="0.0651489641090865" />
      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
    </inertial>
    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
  </link>
  <joint name="left_ankle_pitch_joint" type="revolute">
    <origin xyz="0 0 -0.14" rpy="0 0 0" />
    <parent link="left_knee_pitch" />
    <child link="left_ankle_pitch" />
    <axis xyz="0 1 0" />
    <limit lower="-2" upper="2" effort="20" velocity="15.0" />
  </joint>
  <link name="left_ankle_roll">
    <inertial>
      <origin xyz="0.0149999999999993 -2.77555756156289E-17 -4.94049245958195E-15" rpy="0 0 0" />
      <mass value="0.0282743338823081" />
      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
    </inertial>
    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
  </link>
  <joint name="left_ankle_roll_joint" type="revolute">
    <origin xyz="0 0 -0.0523924267994756" rpy="0 0 0" />
    <parent link="left_ankle_pitch" />
    <child link="left_ankle_roll" />
    <axis xyz="1 0 0" />
    <limit lower="-2" upper="2" effort="20" velocity="15.0" />
  </joint>
  <link name="right_hip_yaw">
    <inertial>
      <origin xyz="-0.0148415027804522 -1.4227820776147E-05 0.00518098759586436" rpy="0 0 0" />
      <mass value="0.22770651071542" />
      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
    </inertial>
    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
  </link>
  <joint name="right_hip_yaw_joint" type="revolute">
    <origin xyz="0 -0.04 0" rpy="0 0 0" />
    <parent link="base" />
    <child link="right_hip_yaw" />
    <axis xyz="0 0 -1" />
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

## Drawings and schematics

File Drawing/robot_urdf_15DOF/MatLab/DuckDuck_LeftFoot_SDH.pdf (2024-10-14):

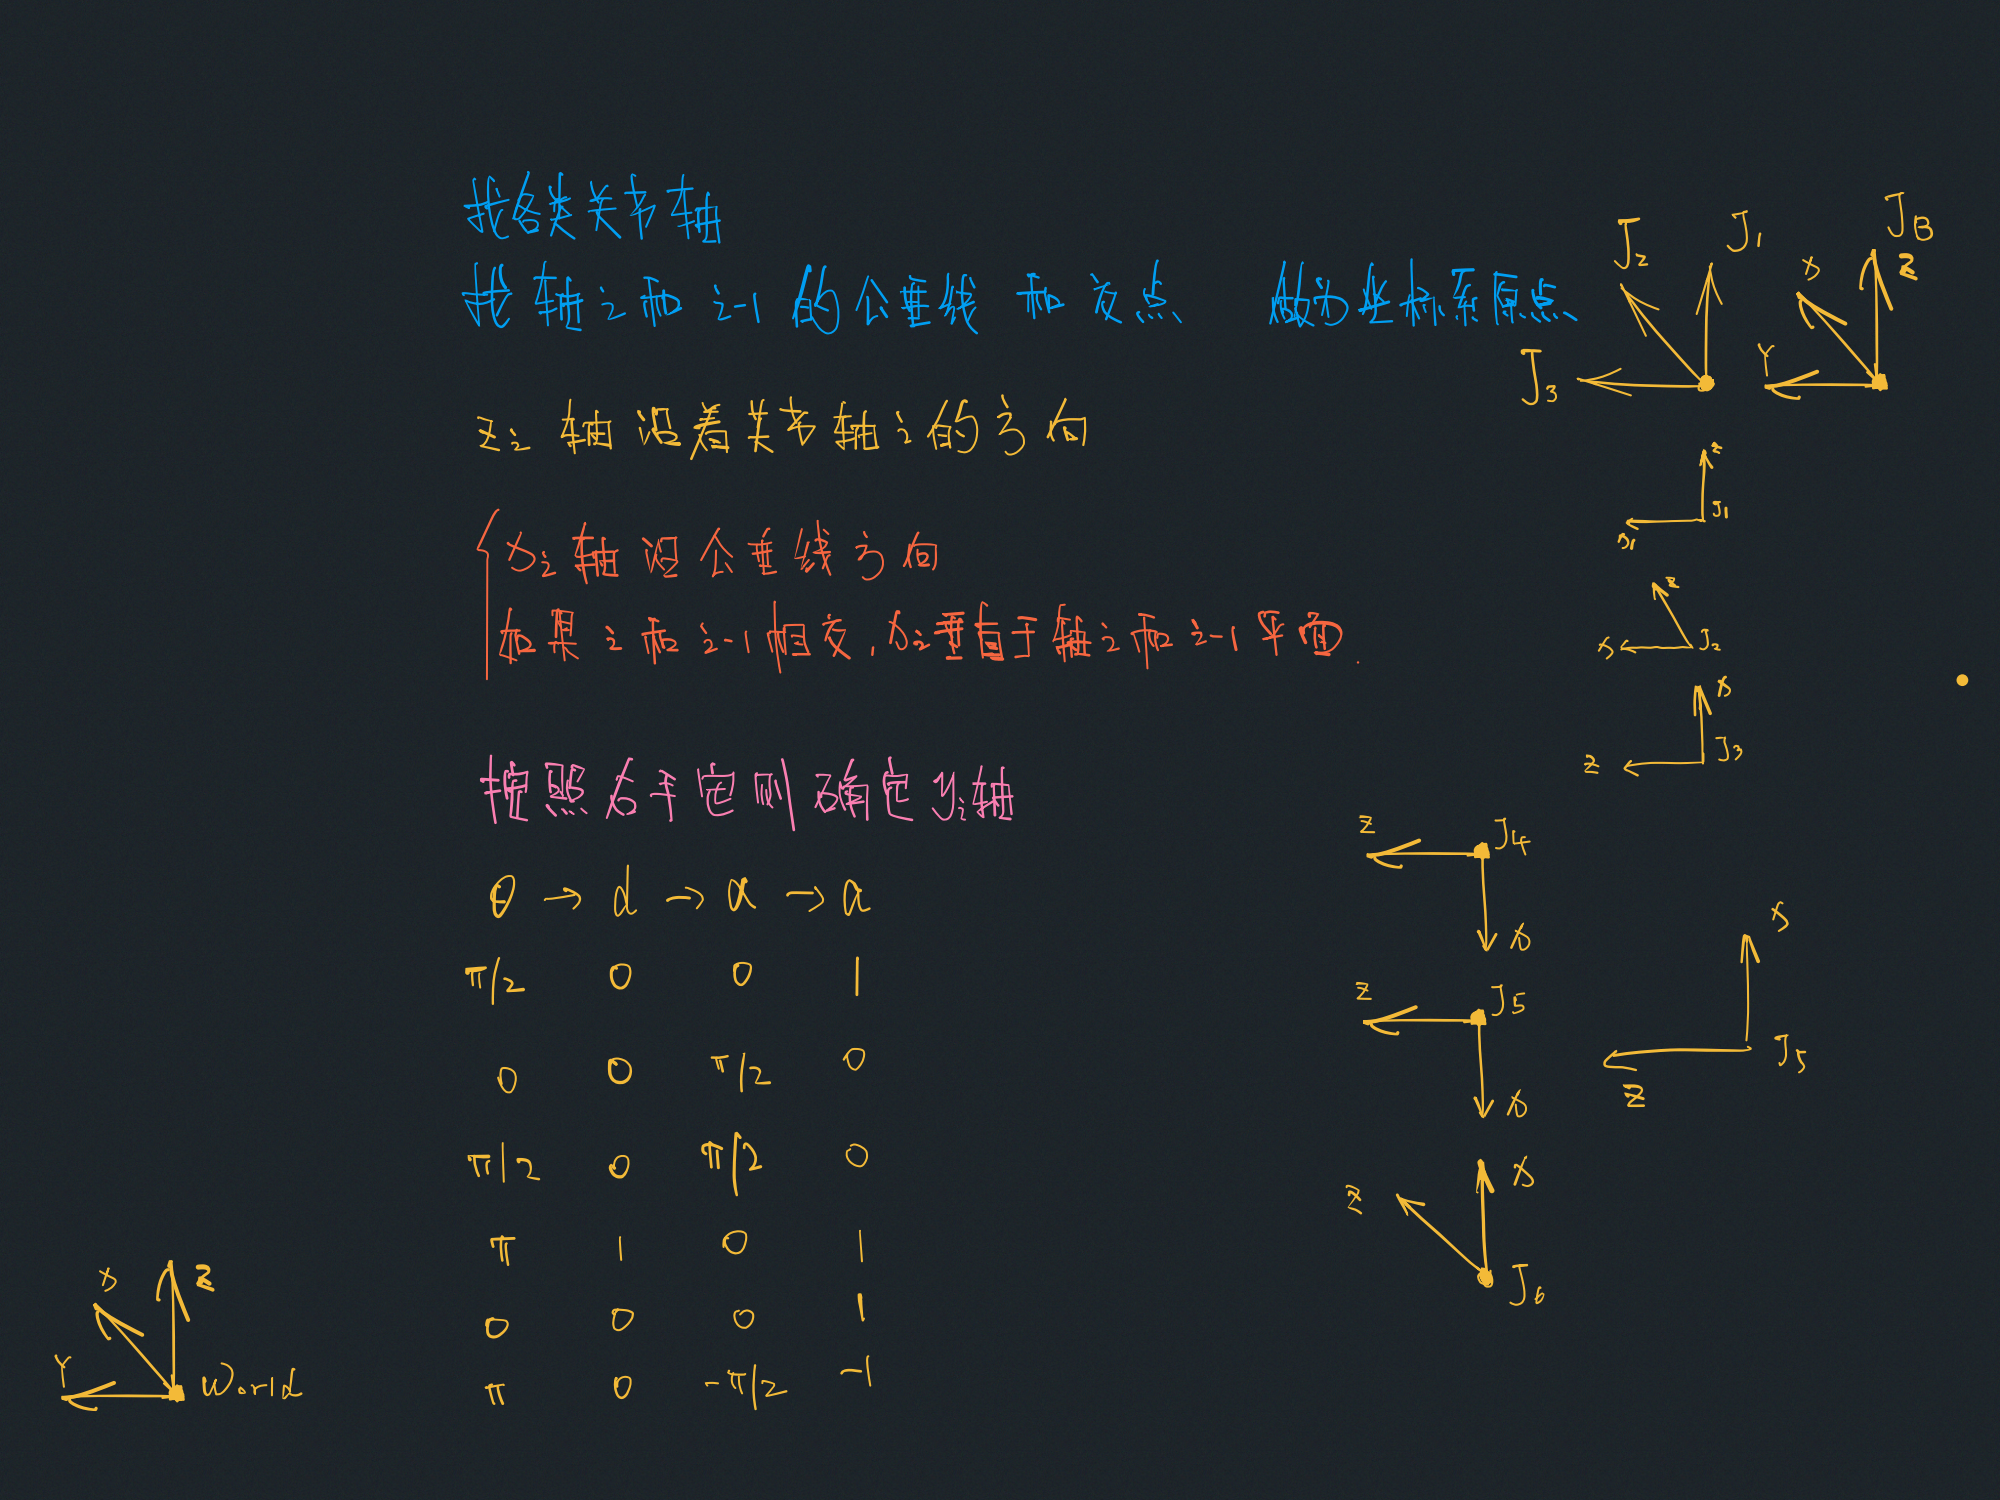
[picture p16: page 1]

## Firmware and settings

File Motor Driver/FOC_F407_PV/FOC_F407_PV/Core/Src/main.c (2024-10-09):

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
/* Includes ------------------------------------------------------------------*/
#include "main.h"
#include "adc.h"
#include "dma.h"
#include "i2c.h"
#include "tim.h"
#include "usart.h"
#include "gpio.h"

/* USER CODE BEGIN Includes */
#include "Serial.h"
#include "myFOC.h"
#include "arm_math.h"
#include "motor.h"
#include "AS5600.h"
#include "IIC_1.h"
/* USER CODE END Includes */

/* USER CODE BEGIN PTD */
extern float Current_Ia;           //Ia??
extern float Current_Ib;           //Ib??
extern float current_Iq;           //Iq??
extern float current_Id;           //Id??
/* USER CODE END PTD */


void SystemClock_Config(void);
/**
  * @brief  The application entry point.
  * @retval int
  */
int main(void)
{
  /* MCU Configuration--------------------------------------------------------*/

  /* Reset of all peripherals, Initializes the Flash interface and the Systick. */
  HAL_Init();

  /* Configure the system clock */
  SystemClock_Config();

  /* Initialize all configured peripherals */
  MX_GPIO_Init();
  MX_DMA_Init();
  MX_ADC1_Init();
  MX_USART1_UART_Init();
  MX_TIM3_Init();
  MX_TIM1_Init();
  MX_I2C2_Init();
  MX_TIM2_Init();
  /* USER CODE BEGIN 2 */
  iic_init();
  adc_uesr_Init();
//  FOC_log("*******  FOC Init!  *******\r\n");
  PWM_Init(); // Enable the PWM output channel of Timx
  HAL_Delay(20);

  Align_Sensor(); // Calibrate the initial electrical Angle

  velocity_PID_Config();
	angle_PID_Config();
  HAL_Delay(50);

  HAL_TIM_Base_Start_IT(&htim3); // Enable TIM3 timer interrupt
//  FOC_log("******  FOC Enter Loop!  *********\r\n");
	HAL_GPIO_WritePin(GPIOF, GPIO_PIN_9, GPIO_PIN_RESET);

  /* USER CODE END 2 */

  /* Infinite loop */
  /* USER CODE BEGIN WHILE */
  while (1)
  {
    /* USER CODE END WHILE */

    /* USER CODE BEGIN 3 */
//		AS5600_log();
    close_Angle_LOG();
//		FOC_log("%f,%f\r\n", Current_Ia, Current_Ib);
//		FOC_log("%f,%f\r\n", current_Iq, current_Id);
  }
  /* USER CODE END 3 */
}

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


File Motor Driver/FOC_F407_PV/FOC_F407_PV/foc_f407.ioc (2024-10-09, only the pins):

Mcu.UserName=STM32F407ZETx
PA0-WKUP.Signal=S_TIM2_CH1_ETR
PA10.Signal=USART1_RX
PA13.Signal=SYS_JTMS-SWDIO
PA14.Signal=SYS_JTCK-SWCLK
PA3.Signal=ADCx_IN3
PA5.Signal=ADCx_IN5
PA9.Signal=USART1_TX
PB10.Signal=GPIO_Output
PB11.Signal=GPIO_Output
PC14-OSC32_IN.Signal=RCC_OSC32_IN
PC15-OSC32_OUT.Signal=RCC_OSC32_OUT
PE11.Signal=S_TIM1_CH2
PE13.Signal=S_TIM1_CH3
PE3.Signal=GPXTI3
PE4.Signal=GPXTI4
PE9.Signal=S_TIM1_CH1
PF0.Signal=I2C2_SDA
PF1.Signal=I2C2_SCL
PF10.Signal=GPIO_Output
PF9.Signal=GPIO_Output
PH0-OSC_IN.Signal=RCC_OSC_IN
PH1-OSC_OUT.Signal=RCC_OSC_OUT

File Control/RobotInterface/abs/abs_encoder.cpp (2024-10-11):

#include "abs_encoder.h"
#include <cmath>
// #include <iostream>
#include <limits>
#include <vector>

PosSensor::PosSensor(double max_range) : max_range_(max_range) {}

double PosSensor::read(double value) { return fmod(value, max_range_); }

DoubleEncoderSystem::DoubleEncoderSystem(double encoder1_gear_ratio,
                                         double encoder2_gear_ratio,
                                         double min_end_detect_pos,
                                         double detect_accuracy,
                                         double encoder1_noise,
                                         double encoder2_noise)
    : encoder1_gear_ratio_(encoder1_gear_ratio),
      encoder2_gear_ratio_(encoder2_gear_ratio),
      min_end_detect_pos_(min_end_detect_pos),
      detect_accuracy_(detect_accuracy), encoder1_noise_(encoder1_noise),
      encoder2_noise_(encoder2_noise) {
  enc1_ptr_ = std::make_unique<PosSensor>(enc1_max_range_);
  enc2_ptr_ = std::make_unique<PosSensor>(enc2_max_range_);

  // get max detect round
  max_dectect_round_ = detect_accuracy_;

  while (fabs(fmod(encoder1_gear_ratio_ * max_dectect_round_, 1)) >
             detect_accuracy_ * encoder1_gear_ratio_ / 360.0 ||
         fabs(fmod(encoder2_gear_ratio_ * max_dectect_round_, 1)) >
             detect_accuracy_ * encoder2_gear_ratio_ / 360.0)
    max_dectect_round_ += detect_accuracy_ / 360.0;
  max_end_detect_pos_ = min_end_detect_pos_ + max_dectect_round_ * 360.0;

  min_end_detect_pos_from_encoder1_ =
      min_end_detect_pos_ + encoder1_noise_ / encoder1_gear_ratio_;
  max_end_detect_pos_from_encoder1_ =
      max_end_detect_pos_ - encoder1_noise_ / encoder1_gear_ratio_;
  min_end_detect_pos_from_encoder2_ =
      min_end_detect_pos_ + encoder2_noise_ / encoder2_gear_ratio_;
  max_end_detect_pos_from_encoder2_ =
      max_end_detect_pos_ - encoder2_noise_ / encoder2_gear_ratio_;

  min_end_detect_pos_ = std::max(min_end_detect_pos_from_encoder1_,
                                 min_end_detect_pos_from_encoder2_);
  max_end_detect_pos_ = std::min(max_end_detect_pos_from_encoder1_,
                                 max_end_detect_pos_from_encoder2_);
}

void DoubleEncoderSystem::SetEncoder1Offset(double offset) {
  encoder1_offset_ = offset;
}

void DoubleEncoderSystem::SetEncoder2Offset(double offset) {
  encoder2_offset_ = offset;
}

void DoubleEncoderSystem::SetEncoder1Dir(int dir) { encoder1_dir_ = dir; }
void DoubleEncoderSystem::SetEncoder2Dir(int dir) { encoder2_dir_ = dir; }

double DoubleEncoderSystem::GetMaxDetectRound() { return max_dectect_round_; }
double DoubleEncoderSystem::GetMinEndDetectPos() { return min_end_detect_pos_; }
double DoubleEncoderSystem::GetMaxEndDetectPos() { return max_end_detect_pos_; }

std::vector<double> DoubleEncoderSystem::GetAllowedEncoderNoise() {
  std::vector<double> allowed_encoder_noise(2);
  double encoder1_read_per_encoder2_cycle =
      enc1_ptr_->read(1 / encoder2_gear_ratio_ * encoder1_gear_ratio_ * 360.0);
  double encoder2_read_per_encoder1_cycle =
      enc2_ptr_->read(1 / encoder1_gear_ratio_ * encoder2_gear_ratio_ * 360.0);

  double encoder1_read_per_end_pos_accuracy =
      enc1_ptr_->read(detect_accuracy_ * encoder1_gear_ratio_);

  double encoder2_read_per_end_pos_accuracy =
      enc2_ptr_->read(detect_accuracy_ * encoder2_gear_ratio_);

  allowed_encoder_noise[0] = std::min(encoder1_read_per_encoder2_cycle,
                                      encoder1_read_per_end_pos_accuracy);
  allowed_encoder_noise[1] = std::min(encoder2_read_per_encoder1_cycle,
                                      encoder2_read_per_end_pos_accuracy);
  return allowed_encoder_noise;
}

double DoubleEncoderSystem::GetEndPos(double encoder1_value,
                                      double encoder2_value) {
  // check validation
  if (encoder1_gear_ratio_ <= 0 || encoder2_gear_ratio_ <= 0)
    return std::numeric_limits<double>::quiet_NaN();

  vec_possible_end_pos_from_encoder1_.clear();
  vec_possible_end_pos_from_encoder2_.clear();

  double end_pos = std::numeric_limits<double>::quiet_NaN();

  double end_pos_per_encoder1_read = encoder1_dir_ / encoder1_gear_ratio_;
  double end_pos_per_encoder2_read = encoder2_dir_ / encoder2_gear_ratio_;
  double possible_end_pos_from_encoder1 =
      (encoder1_value - encoder1_offset_) * end_pos_per_encoder1_read;
  double possible_end_pos_from_encoder2 =
      (encoder2_value - encoder2_offset_) * end_pos_per_encoder2_read;

  // std::cout << "possible_end_pos_from_encoder1: "
  //           << possible_end_pos_from_encoder1 << std::endl;
  // std::cout << "possible_end_pos_from_encoder2: "
  //           << possible_end_pos_from_encoder2 << std::endl;

  // get possible end positions from encoder1
  for (double end_pos_from_encoder1 =
           possible_end_pos_from_encoder1 - 360.0 / encoder1_gear_ratio_;
       end_pos_from_encoder1 >= min_end_detect_pos_;
       end_pos_from_encoder1 -= 360.0 / encoder1_gear_ratio_) {
    vec_possible_end_pos_from_encoder1_.insert(
        vec_possible_end_pos_from_encoder1_.begin(), end_pos_from_encoder1);
  }
  for (double end_pos_from_encoder1 = possible_end_pos_from_encoder1;
       end_pos_from_encoder1 <= max_end_detect_pos_;
       end_pos_from_encoder1 += 360.0 / encoder1_gear_ratio_) {
    vec_possible_end_pos_from_encoder1_.push_back(end_pos_from_encoder1);
  }
  // std::cout << "possible_end_pos_from_encoder1:" << std::endl;
  // for (auto possible_end_pos_from_encoder1 :
  //      vec_possible_end_pos_from_encoder1_) {
  //   std::cout << possible_end_pos_from_encoder1 << "\t";
  // }
  // std::cout << std::endl;
  // get possible end positions from encoder2
  for (double end_pos_from_encoder2 =
           possible_end_pos_from_encoder2 - 360.0 / encoder2_gear_ratio_;
       end_pos_from_encoder2 >= min_end_detect_pos_;
       end_pos_from_encoder2 -= 360.0 / encoder2_gear_ratio_) {
    vec_possible_end_pos_from_encoder2_.insert(
        vec_possible_end_pos_from_encoder2_.begin(), end_pos_from_encoder2);
  }
  for (double end_pos_from_encoder2 = possible_end_pos_from_encoder2;
       end_pos_from_encoder2 <= max_end_detect_pos_;
       end_pos_from_encoder2 += 360.0 / encoder2_gear_ratio_) {
    vec_possible_end_pos_from_encoder2_.push_back(end_pos_from_encoder2);
  }
  // std::cout << "possible_end_pos_from_encoder2:" << std::endl;
  // for (auto possible_end_pos_from_encoder2 :
  //      vec_possible_end_pos_from_encoder2_) {
  //   std::cout << possible_end_pos_from_encoder2 << "\t";
  // }
  // std::cout << std::endl;

  for (auto i = 0; i < vec_possible_end_pos_from_encoder1_.size(); i++) {
    for (auto j = 0; j < vec_possible_end_pos_from_encoder2_.size(); j++) {
      if (fabs(vec_possible_end_pos_from_encoder1_[i] -
               vec_possible_end_pos_from_encoder2_[j]) < detect_accuracy_) {
        end_pos = vec_possible_end_pos_from_encoder1_[i];
        return end_pos;
      }
    }
  }

  return end_pos;
}

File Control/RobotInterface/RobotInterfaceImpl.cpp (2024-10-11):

#include "RobotInterfaceImpl.h"

RobotInterfaceImpl::RobotInterfaceImpl() {
#ifdef STATE_ESTIMATE
  stateEstimate_ = new StateEstimate;
#endif
  error_state_ = false;
#ifndef WEBOTS
  funS2P = new functionIKID_S2P;
  jointInterface_ = new JointInterface;
#endif
}

void RobotInterfaceImpl::Init() {
  int i;
#ifdef WEBOTS
  // webots init
  humanoid.initWebots();
#else

  // joint name
  i = 0;
  joint_name_.resize(joint_num_);
  joint_name_[i] = "hipPitch_Left";
  i++;
  joint_name_[i] = "hipRoll_Left";
  i++;
  joint_name_[i] = "hipYaw_Left";
  i++;
  joint_name_[i] = "kneePitch_Left";
  i++;
  joint_name_[i] = "anklePitch_Left";
  i++;
  joint_name_[i] = "ankleRoll_Left";
  i++;

  joint_name_[i] = "hipPitch_Right";
  i++;
  joint_name_[i] = "hipRoll_Right";
  i++;
  joint_name_[i] = "hipYaw_Right";
  i++;
  joint_name_[i] = "kneePitch_Right";
  i++;
  joint_name_[i] = "anklePitch_Right";
  i++;
  joint_name_[i] = "ankleRoll_Right";
  i++;

  joint_name_[i] = "waistRoll";
  i++;
  joint_name_[i] = "waistPitch";
  i++;
  joint_name_[i] = "waistYaw";
  i++;

  joint_name_[i] = "shoulderPitch_Left";
  i++;
  joint_name_[i] = "shoulderRoll_Left";
  i++;
  joint_name_[i] = "shoulderYaw_Left";
  i++;
  joint_name_[i] = "elbow_Left";
  i++;

  if (adam_type == ADAM_TYPE::AdamLite) {
  } else if (adam_type == ADAM_TYPE::AdamStandard) {
    joint_name_[i] = "wristYaw_Left";
    i++;
    joint_name_[i] = "wristPitch_Left";
    i++;
    joint_name_[i] = "wristRoll_Left";
    i++;
  } else if (adam_type == ADAM_TYPE::StandardPlus23) {
  } else if (adam_type == ADAM_TYPE::StandardPlus29) {
    joint_name_[i] = "wristYaw_Left";
    i++;
    joint_name_[i] = "wristPitch_Left";
    i++;
    joint_name_[i] = "wristRoll_Left";
    i++;
  } else if (adam_type == ADAM_TYPE::StandardPlus53) {
  }

  joint_name_[i] = "shoulderPitch_Right";
  i++;
  joint_name_[i] = "shoulderRoll_Right";
  i++;
  joint_name_[i] = "shoulderYaw_Right";
  i++;
  joint_name_[i] = "elbow_Right";
  i++;

  if (adam_type == ADAM_TYPE::AdamLite) {
  } else if (adam_type == ADAM_TYPE::AdamStandard) {
    joint_name_[i] = "wristYaw_Right";
    i++;
    joint_name_[i] = "wristPitch_Right";
    i++;
    joint_name_[i] = "wristRoll_Right";
    i++;
  } else if (adam_type == ADAM_TYPE::StandardPlus23) {
  } else if (adam_type == ADAM_TYPE::StandardPlus29) {
    joint_name_[i] = "wristYaw_Right";
    i++;
    joint_name_[i] = "wristPitch_Right";
    i++;
    joint_name_[i] = "wristRoll_Right";
    i++;
  } else if (adam_type == ADAM_TYPE::StandardPlus53) {
  }
  // if(adam_type==ADAM_TYPE::AdamLite){
  // }else if(adam_type==ADAM_TYPE::AdamStandard){
  // }else if(adam_type==ADAM_TYPE::StandardPlus23){
  // }else if(adam_type==ADAM_TYPE::StandardPlus29){
  // }else if(adam_type==ADAM_TYPE::StandardPlus53){
  // }
  absolute_pos_init_ = Eigen::VectorXd::Zero(joint_num_);
  absolute_pos_zero_ = Eigen::VectorXd::Zero(joint_num_);
  absolute_pos_dir_ = Eigen::VectorXd::Zero(joint_num_);
  absolute_pos_gear_ratio_ = Eigen::VectorXd::Zero(joint_num_);
  motor_rotor_abs_pos_ = Eigen::VectorXd::Zero(joint_num_);
  motor_rotor_cur_pos_ = Eigen::VectorXd::Zero(joint_num_);
  joint_Kp_ = Eigen::VectorXd::Zero(joint_num_);
  joint_Kd_ = Eigen::VectorXd::Zero(joint_num_);

  ReadAbsEncoder(absolute_pos_init_, motor_rotor_cur_pos_);

  // read joint_pd_config json
  QFile loadFile_pd("Sources/config/joint_pd_config.json");
  if (!loadFile_pd.open(QIODevice::ReadOnly)) {
    qDebug() << "couldn't open joint_pd_config json";
    return;
  }

  QByteArray all_data_pd = loadFile_pd.readAll();
  loadFile_pd.close();

  QJsonParseError json_error_pd{};
  QJsonDocument doc_pd(QJsonDocument::fromJson(all_data_pd, &json_error_pd));

  if (json_error_pd.error != QJsonParseError::NoError) {
    qDebug() << "json error!" << json_error_pd.errorString();
    return;
  }

  if (!doc_pd.isNull() && json_error_pd.error == QJsonParseError::NoError) {
    if (doc_pd.isObject()) {
      QJsonObject object = doc_pd.object();
      for (int i = 0; i < joint_num_; i++) {
        bool find_flag = false;
        QJsonObject::iterator it = object.begin();
        // read the dimension of the variables
        while (it != object.end()) {
          if (it.key() == QString::fromStdString(joint_name_[i])) {
            find_flag = true;
            QJsonObject it_object = it.value().toObject();
            QJsonObject::iterator iter = it_object.begin();
            while (iter != it_object.end()) {
              // if (iter.key() == "absolute_pos_zero") {
              //   absolute_pos_zero_(i) = iter.value().toDouble();
              // }
              if (iter.key() == "control_config") {
                QJsonObject iter_object = iter.value().toObject();
                QJsonObject::iterator config_it = iter_object.begin();
                while (config_it != iter_object.end()) {
                  if (config_it.key() == "Kp") {
                    joint_Kp_[i] = config_it.value().toDouble();
                  }
                  if (config_it.key() == "Kd") {
                    joint_Kd_[i] = config_it.value().toDouble();
                  }
                  config_it++;
                }
              }
              iter++;
            }
          }
          it++;
        }
        if (!find_flag) {
          std::cout << "joint " << joint_name_[i] << " not found!" << std::endl;
        }
      }
    }
  }

  // read standard_joint_abs_config json
  // QFile loadFile_abs("Sources/config/standard_joint_abs_config.json");
  QString path = "/root/.adam/joint_abs_config.json";
  QFile loadFile_abs(path);  // change to local default path
  if (!loadFile_abs.open(QIODevice::ReadOnly)) {
    qDebug() << "couldn't open joint_abs_config json";
    return;
  }

  QByteArray all_data_abs = loadFile_abs.readAll();
  loadFile_abs.close();

  QJsonParseError json_error_abs{};
  QJsonDocument doc_abs(QJsonDocument::fromJson(all_data_abs, &json_error_abs));
  if (json_error_abs.error != QJsonParseError::NoError) {
    qDebug() << "json error!" << json_error_abs.errorString();
    return;
  }
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

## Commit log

2024-10-09 update files
    [4310-36.SLDPRT, 4310-36.STL, 6010-36.SLDPRT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]
2024-10-10 1.add DuckDuck-13DOF files 2.update ReadME.md file
    [DuckDuck.csv, DuckDuck.urdf, base.STL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]
2024-10-10 update robot_urdf_15DOF files
    [DuckDuck.SLDASM, DuckDuck.csv, DuckDuck.urdf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]
2024-10-10 add DuckDuck-15DOF webots files
    [DuckDuck.csv, DuckDuck.urdf, base.STL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]
2024-10-11 1.use last PND mpc controller 2.update adam_lite_simple and DuckDuck model files
    [DuckDuck.urdf, adam_lite.urdf, adam_lite_simple.urdf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]
2024-10-14 test interative inverse kinematic
2024-10-16 Change joints positive direction for DuckDuck right leg
    The DuckDuck zero statue is ok and add control for head
    set rosopen is TRUE and compile for ros
    [DuckDuck.urdf]
2024-10-16 update rqt_multiplot JointState.xml file
2024-10-16 Update Drawing .gitignore file
    Add DuckDuck_Init_Position.SLDASM file for zero state
    [DuckDuck.SLDASM, DuckDuck_Init_Position.SLDASM, calf.SLDPRT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]
2024-10-17 fix IK iteration can get solution
    change euler ZYX to XYZ
    add urdfreader to check body and joint
    add jocabi in zero state
2024-10-17 Z2S state not ok, still need to fix problem of wrong order for urdfreader
    fix limit and boundingObject for DuckDuck.urdf and DuckDuck.wbt
    add Z2S state bug recode
    add test for zero state position jacobi in read_urdf.cpp
    fix JointState_left_leg_v.xml
    add Z2S and stand in state.cpp, but not test stand
    [DuckDuck.urdf]
2024-10-18 fix problem of wrong joint order use tool of urdfreader read urdf files
    check jacobi matrix and pose right
    fix dataPub joint_name
    change paras for joint PD and about wbc process
    [DuckDuck.urdf, throat_pitch.STL, throat_roll.STL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]

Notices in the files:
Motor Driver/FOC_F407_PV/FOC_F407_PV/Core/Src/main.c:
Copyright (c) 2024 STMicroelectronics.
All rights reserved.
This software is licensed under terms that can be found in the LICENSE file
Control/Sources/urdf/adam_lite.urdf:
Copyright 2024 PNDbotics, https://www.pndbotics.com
